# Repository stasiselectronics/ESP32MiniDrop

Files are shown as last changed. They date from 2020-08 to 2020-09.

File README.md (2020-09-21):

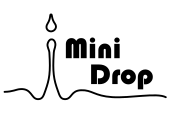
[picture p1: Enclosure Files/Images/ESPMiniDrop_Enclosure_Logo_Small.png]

# ESP32MiniDrop
This repository contains the source files for a DIY Bluetooth connected solenoid controller for use with water drop photography. This project is still a work in progress, so make sure to follow and keep up with any future updates!

[Check out the project's companion page for even more details!](https://chandlermccowan.github.io/ESP32MiniDrop/)

## Quick Links
- [Board Schematics (download)](https://github.com/ChandlerMcCowan/ESP32MiniDrop/raw/master/Hardware%20Files/PDFs/ESP32MiniDrop_Schematics_A02.pdf)
- [Board Drawing (download)](https://github.com/ChandlerMcCowan/ESP32MiniDrop/raw/master/Hardware%20Files/PDFs/ESP32MiniDrop_Assembly_A02.pdf)
- [Enclosure Drawing (download)](https://github.com/ChandlerMcCowan/ESP32MiniDrop/raw/master/Enclosure%20Files/ESP32MiniDrop_Enclosure_Assembly_Drawing.pdf)

## Current Status

This project is still in its early stages, so this repository should be considered a work in progress. As of now, here is what has been done:
- Finalizing schematic and board design for revision A02
- First rounds of iterations on 3D printed parts for enclosure and solenoid stand
- Completed basic function testing for revision A01
- Test firmware developed for ESP32 to use Bluetooth serial communication to pass JSON objects for control and configuration

## Future Goals

Here's what needs to get done for this project:
- Develop firmware to enable connection to Android/iOS app
- Develop Android/iOS app
- Perform electrical tests on board design

## Usage
The goal for this device is to help make water drop photography a snap. Water drop photography focuses on macro shots of water or other liquids at various stages of impact. This controller enables you to use an electronically controlled valve (i.e. solenoid) positioned above a pool of liquid, where you can adjust the timing between succesive drops, the size of the drops themselves, and when to tell the camera to take the picture. By connecting your phone to the controller, you'll be able to dial in these settings and get significantly more repeatable shots than with manual methods.

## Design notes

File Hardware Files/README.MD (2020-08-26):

# ESP32MiniDrop Hardware Files
Designed in KiCad 5.1.6 

This folder contains the source files for the PCB design of the ESP32MiniDrop, along with supporting documentation. Here you can find PDFs of the schematic, an assembly drawing, and gerbers used for fabrication. 

The board design is centered around the ESP32 WROOM 32D module. This has WiFi and Bluetooth included, which helps to reduce the auxillary components needed. The board has one screw terminal to attach bare wires to hook up the solenoid coil. The solenoid is controlled with a MOSFET with flyback diode attached. 

To help load Arduino sketches onto the board, an USB to UART IC is included in the design. This takes the USB data lines and converts them to the RS232 UART signals going to the ESP32. When programming, the script used to flash the chip will take advantage of the DTR and RTS signals to put the EPS32 into boot mode and automatically reset when done. 

**NOTE**
This board uses 0603 passive components and small outline packages, so a patient hand and good eyes (or a microscope) will be needed to hand solder. The CP2012N is in a Quad Flat no Lead (QFN) package, and is not an easy part to attach. You can skip the USB to UART chip and instead use the 0.100" programming headers (J5) to load the sketches on the ESP32 manually.

## Overview
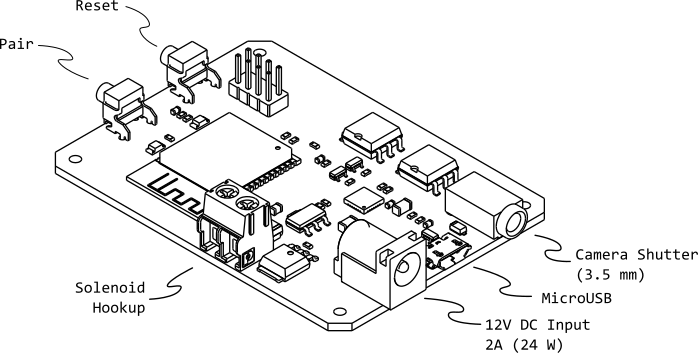
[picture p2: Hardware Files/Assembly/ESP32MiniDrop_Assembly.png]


## Bill of Materials
| Reference Designator | Value | Quantity | Manufacturer | Part Number |
|---|---|:---:|---|---:|
| C1, C3 | 0.1uF 50V | 2 | Yageo | CC0603ZRY5V9BB104 |
| C2, C5, C7 | 10uF 50V | 3 | Samsung Electro-Mechanics | CL31A106MBHNNNE |
| C4 C6 | 1nF 50V | 2 | Yageo | CC0603KRX7R9BB102 |
| C8 | 1uF 50V | 1 | Yageo | CC0603KRX5R9BB105 |
| C9 | 22uF 6.3V | 1 | Samsung Electro-Mechanics | CL21A226MQQNNNE |
| D1, D6 | 40V 2A | 2 | ON Semiconductor | SS24FL |
| D2 | SP0502BAHT | 1 | Littelfuse Inc. | SP0502BAHTG |
| D3 | GREEN 3.2V 20mA | 1 | Wurth Elektronik | 150120GS75000 |
| D4 | BLUE 3.2V 20mA | 1 | Wurth Elektronik | 150120BS75000 |
| D5 | 20V 1A | 1 | ON Semiconductor | MBR120VLSFT3G |
| D7 | 600V 5A | 1 | SMC Diode Solutions | SD560BTR |
| J1 | USB_B_Mini | 1 | Molex | 1050170001 |
| J2 | Barrel_Jack | 1 | CUI Devices | PJ-037A |
| J3 | AudioJack | 1 | Kycon, Inc. | STX-3000 |
| J4 | Solenoid Terminal  | 1 | Pheonix Contact | 1935161 |
| Q1 Q2 | S8050 | 2 | ON Semiconductor | MMBT2222ALT1G |
| Q3 | NMOS 60V 46A | 1 | ON Semiconductor | NTD5865NLT4G |
| R1, R2, R6, R7, R10, R13, R16 | 10k 1% 0.1W | 7 | Yageo | RC0603FR-0710KL |
| R14, R15 | 220R 1% 0.1W | 2 | Yageo | RC0603FR-07220RL |
| R3 | 22.1K 1% 0.1W | 1 | Yageo | RC0603FR-0722K1L |
| R4 | 47.5K 1% 0.1W | 1 | Yageo | RC0603FR-0747K5L |
| R5 | 2K 1% 0.1W | 1 | Yageo | RC0603FR-072KL |
| R8, R9, R11, R12 | 0R 0.1W | 4 | Yageo | 311-0.0GRCT-ND |
| SW1 | SPST (RED) | 1 | TE Connectivity ALCOSWITCH Switches | 1825027-6 |
| SW2 | SPST (BLUE) | 1 | TE Connectivity ALCOSWITCH Switches | 1825027-8 |
| U1 | CP2102N-A01-GQFN28 | 1 | Silicon Labs | CP2102N-A02-GQFN28R |
| U2 | AZ1117-3.3 | 1 | Diodes Incorporated | AZ1117CH-3.3TRG1 |
| U3 | ESP32-WROOM-32 | 1 | Espressif | ESP32-WROOM-32D |
| U4, U5 | 4N25 | 2 | Broadcom Limited | 4N25-500E |

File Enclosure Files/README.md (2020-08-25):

# Enclosure

Designed in FreeCAD 0.18

Here are the design files for a 3D printable plastic enclosure for the ESP32MiniDrop. There are two pieces, a Top and Bottom. STEP files are included to help visualize the pieces, feel free to 

## Printing
To start 3D printing, download the STL Files or modify the CAD files and export to STL.

A test print is planned and will be reported here. 

Using Prusa Slicer 2.2.0 with the following settings gives a print time of 5h 12m
- Layer Height | 0.10mm Detail 
- Filament     | Generic PLA   
- Supports     | None          
- Infill       | 80%           

## Overview
Here is an orhtographic view of the assembled case, along with a size comparison to a Sony DSLR and 12V Solenoid Valve. 

Light pipes for the two status LEDs can be created using 3mm diameter acrylic rods, cut to 12mm and inserted into the top piece.

There are 4 M2 Screw holes that for now just self tap into the top section plastic. Threaded inserts would be great addition, or maybe an embedded nut. Screw length should be between 6mm and 8mm.

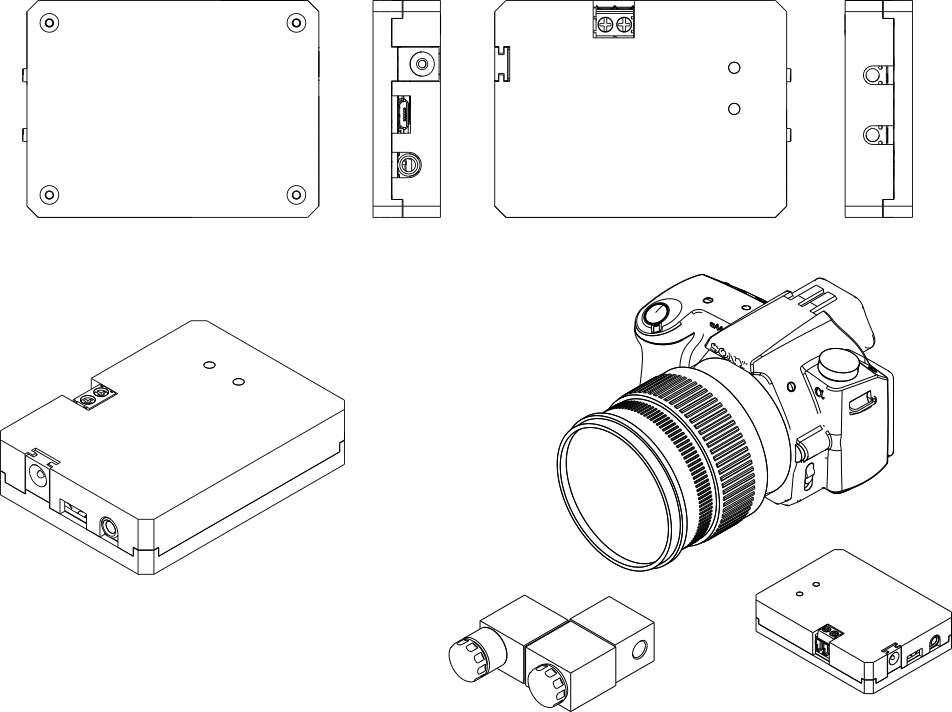
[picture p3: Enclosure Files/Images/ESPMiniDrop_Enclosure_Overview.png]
[]()

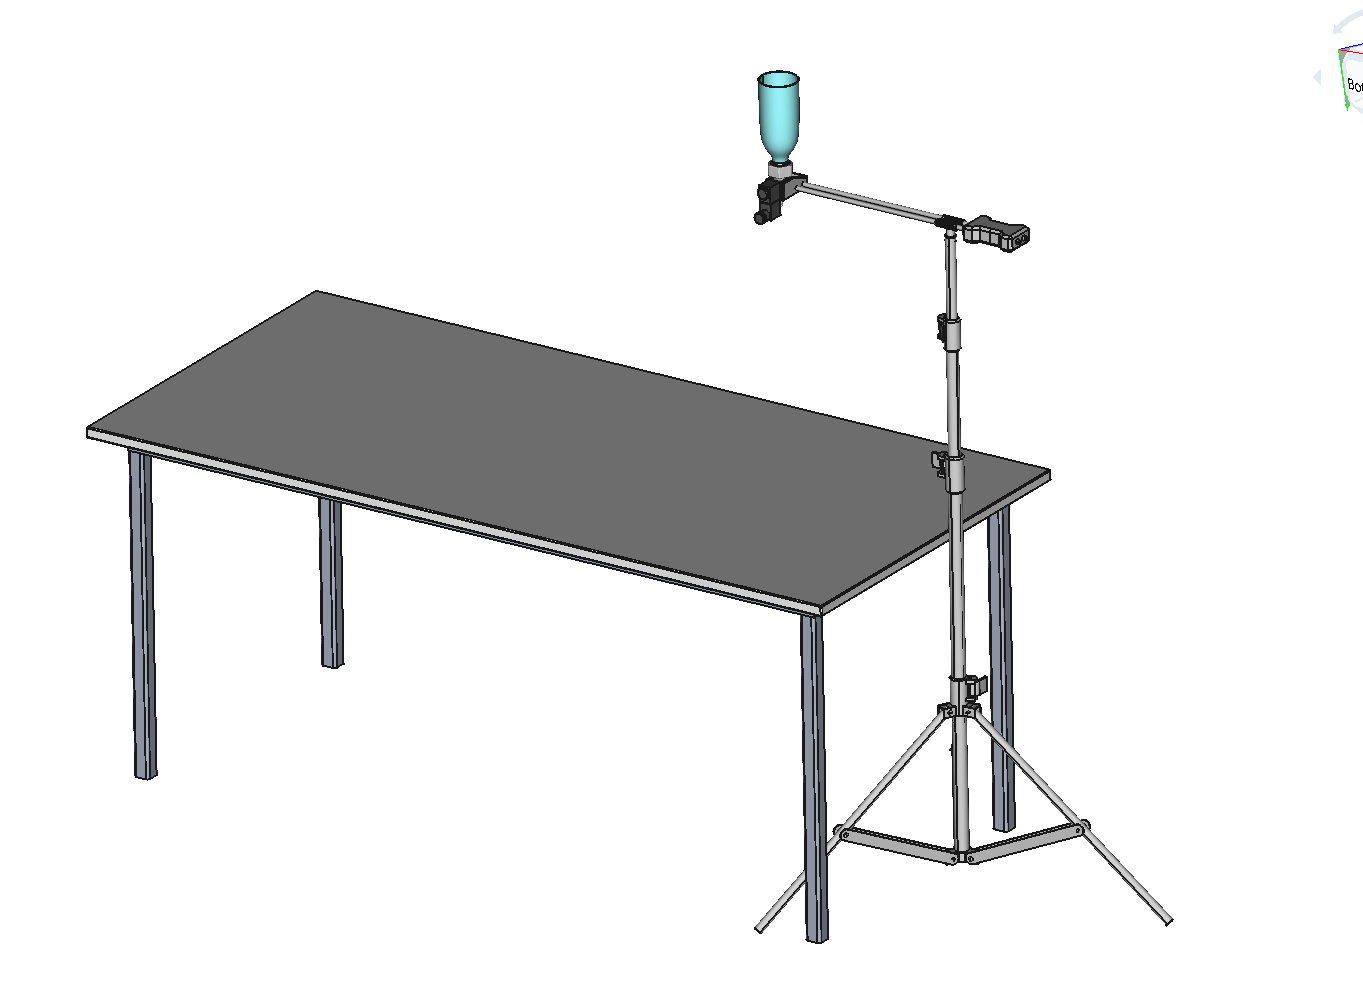
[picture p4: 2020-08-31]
Stand Files/Images/StandWithTable.png

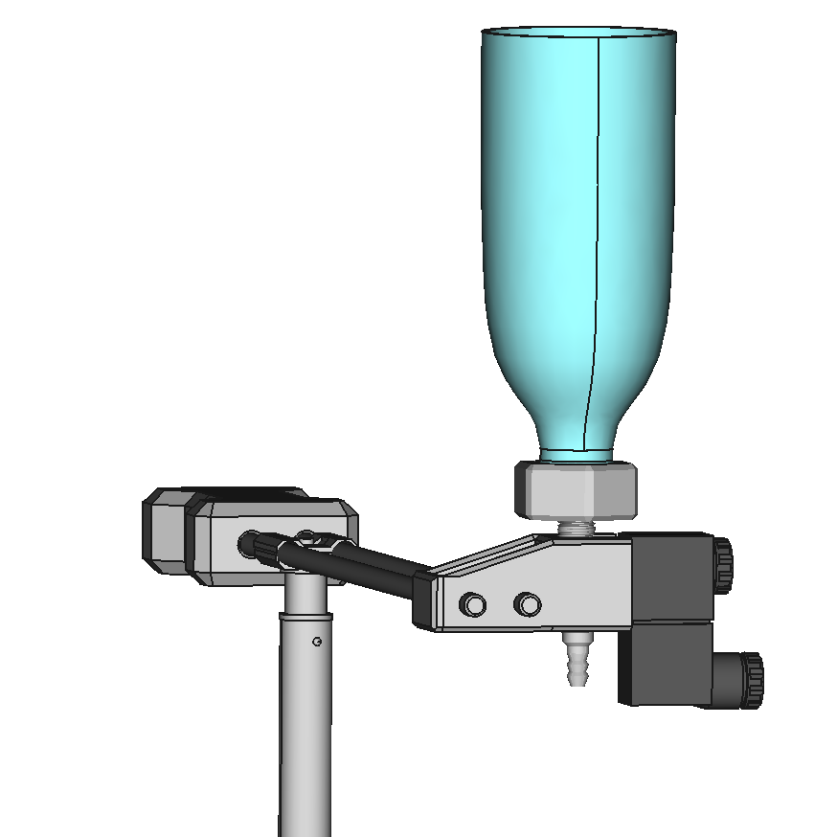
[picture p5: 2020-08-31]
Stand Files/Images/bracke_closeup.png

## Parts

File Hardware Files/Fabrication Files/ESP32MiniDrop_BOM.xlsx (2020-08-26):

Project Name | ESP32MiniDrop | Rev | A02
Reference Designator | Description | Manufactuer | Part Number | Quantity
C1, C3 | 0.1uF 50V | Yageo | CC0603ZRY5V9BB104 | 2
C2, C5, C7 | 10uF 50V | Samsung Electro-Mechanics | CL31A106MBHNNNE | 3
C4 C6 | 1nF 50V | Yageo | CC0603KRX7R9BB102 | 2
C8 | 1uF 50V | Yageo | CC0603KRX5R9BB105 | 1
C9 | 22uF 6.3V | Samsung Electro-Mechanics | CL21A226MQQNNNE | 1
D1, D6 | 40V 2A | ON Semiconductor | SS24FL | 2
D2 | SP0502BAHT | Littelfuse Inc. | SP0502BAHTG | 1
D3 | GREEN 3.2V 20mA | Wurth Elektronik | 150120GS75000 | 1
D4 | BLUE 3.2V 20mA | Wurth Elektronik | 150120BS75000 | 1
D5 | 20V 1A | ON Semiconductor | MBR120VLSFT3G | 1
D7 | 600V 5A | SMC Diode Solutions | SD560BTR | 1
J1 | USB_B_Mini | Molex | 1050170001 | 1
J2 | Barrel_Jack | CUI Devices | PJ-037A | 1
J3 | AudioJack | Kycon, Inc. | STX-3000 | 1
J4 | Solenoid Terminal | Pheonix Contact | 1935161 | 1
Q1 Q2 | S8050 | ON Semiconductor | MMBT2222ALT1G | 2
Q3 | NMOS 60V 46A | ON Semiconductor | NTD5865NLT4G | 1
R1, R2, R6, R7, R10, R13, R16 | 10k 1% 0.1W | Yageo | RC0603FR-0710KL | 7
R14, R15 | 220R 1% 0.1W | Yageo | RC0603FR-07220RL | 2
R3 | 22.1K 1% 0.1W | Yageo | RC0603FR-0722K1L | 1
R4 | 47.5K 1% 0.1W | Yageo | RC0603FR-0747K5L | 1
R5 | 2K 1% 0.1W | Yageo | RC0603FR-072KL | 1
R8, R9, R11, R12 | 0R 0.1W | Yageo | 311-0.0GRCT-ND | 4
SW1 | SPST (RED) | TE Connectivity ALCOSWITCH Switches | 1825027-6 | 1
SW2 | SPST (BLUE) | TE Connectivity ALCOSWITCH Switches | 1825027-8 | 1
U1 | CP2102N-A01-GQFN28 | Silicon Labs | CP2102N-A02-GQFN28R | 1
U2 | AZ1117-3.3 | Diodes Incorporated | AZ1117CH-3.3TRG1 | 1
U3 | ESP32-WROOM-32 | Espressif | ESP32-WROOM-32D | 1
U4, U5 | 4N25 | Broadcom Limited | 4N25-500E | 2

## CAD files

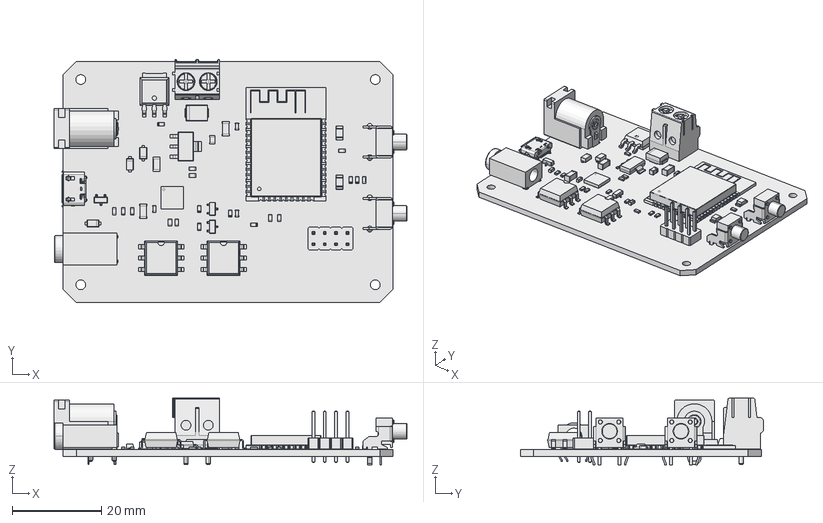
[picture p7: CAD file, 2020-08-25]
Hardware Files/Assembly/ESP32MiniDrop_Assembly.FCStd
79.1 x 54.5 x 14.9 mm

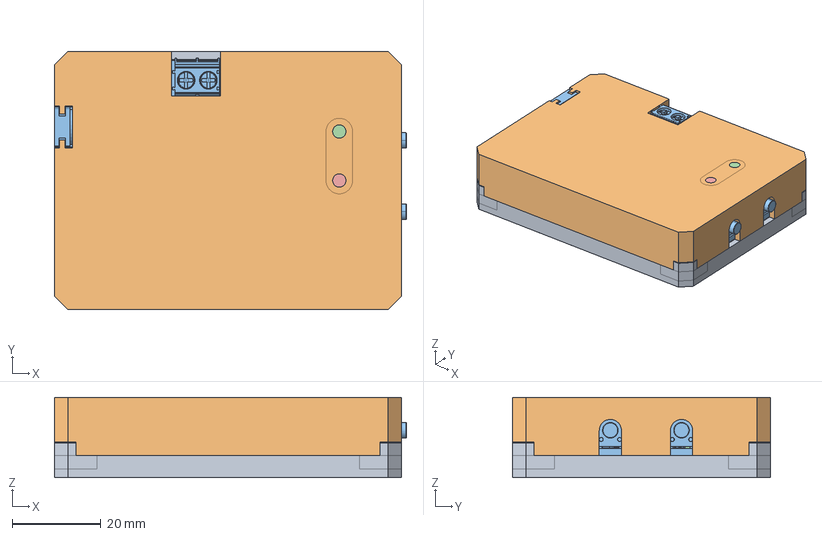
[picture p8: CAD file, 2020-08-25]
Enclosure Files/CAD Files/ESPMiniDrop_Enclosure_Assembly.FCStd
79.1 x 58.0 x 18.1 mm
ESPMiniDrop_Enclosure_Bottom_001
ESPMiniDrop_Enclosure_001
ESP32MiniDrop_PCBA1_001
ESPMiniDrop_Enclosure_LightPipe_001
ESPMiniDrop_Enclosure_LightPipe_002

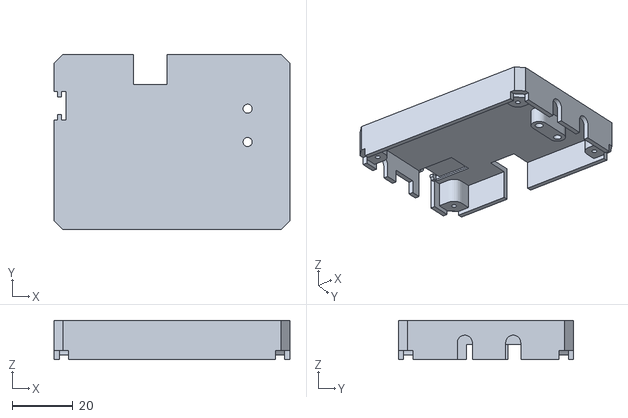
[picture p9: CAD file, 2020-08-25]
Enclosure Files/STL Files/ESP32MiniDrop_Enclosure_Top.stl
78.0 x 58.0 x 13.0

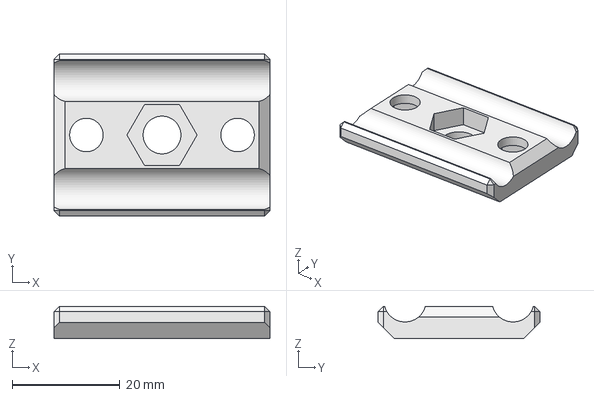
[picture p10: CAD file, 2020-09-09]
Stand Files/CAD Files/ESP32MiniDrop_Stand_TripodClampBtm.FCStd
40.0 x 30.0 x 6.00 mm

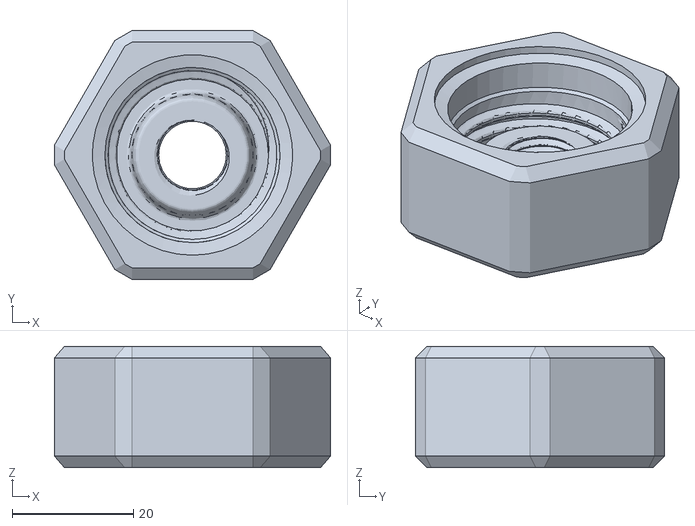
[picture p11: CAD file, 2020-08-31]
Stand Files/STL Files/ESP32MiniDrop_Stand_BottleAdapter.stl
45.4 x 41.0 x 20.0

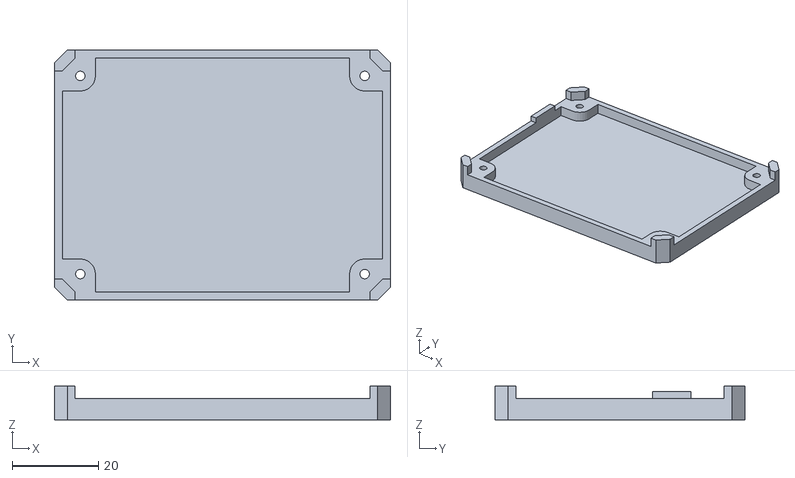
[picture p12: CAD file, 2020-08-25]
Enclosure Files/STL Files/ESP32MiniDrop_Enclosure_Bottom.stl
78.0 x 58.0 x 7.80

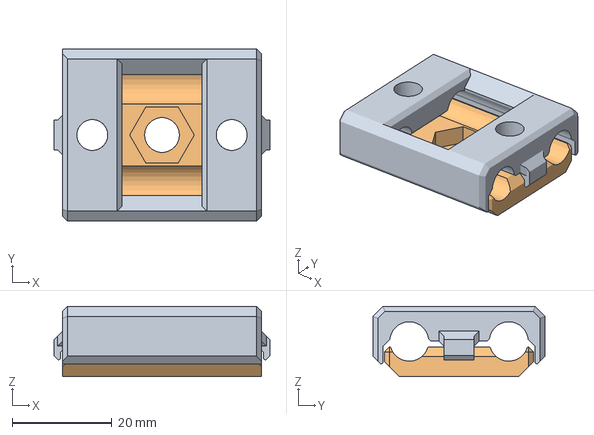
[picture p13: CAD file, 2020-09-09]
Stand Files/CAD Files/ESP32MiniDrop_Stand_TripodClampTop.FCStd
43.4 x 34.6 x 14.1 mm
ESP32MiniDrop_Stand_TripodClampBtm

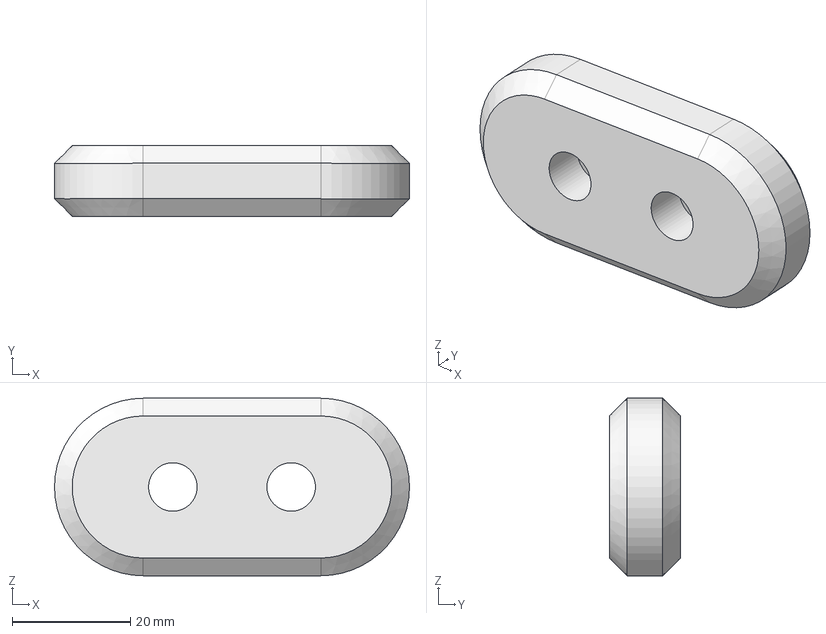
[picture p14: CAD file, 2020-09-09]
Stand Files/CAD Files/ESP32MiniDrop_Stand_RodEnd.FCStd
60.0 x 12.0 x 30.0 mm

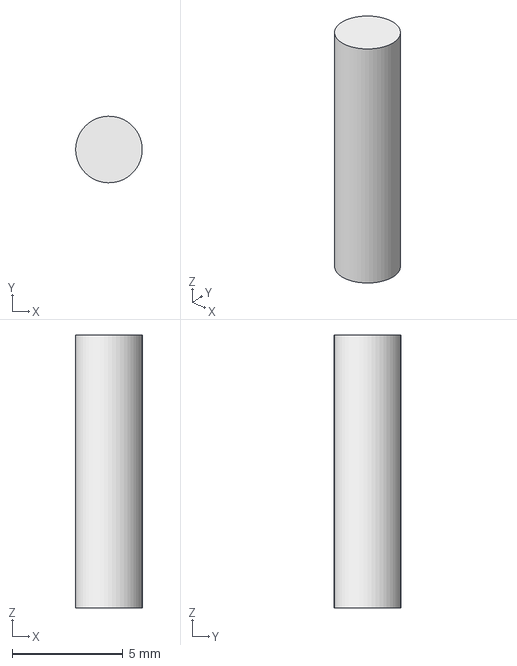
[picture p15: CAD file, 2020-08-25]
Enclosure Files/CAD Files/ESPMiniDrop_Enclosure_LightPipe.FCStd
3.00 x 3.00 x 12.3 mm

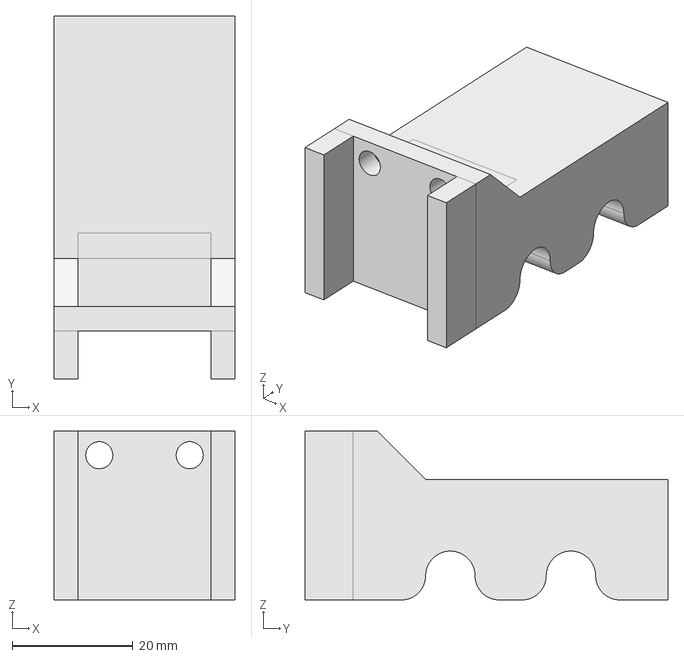
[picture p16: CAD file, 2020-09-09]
Stand Files/CAD Files/ESP32MiniDrop_Stand_SolenoidBracket.FCStd
30.0 x 60.2 x 28.0 mm

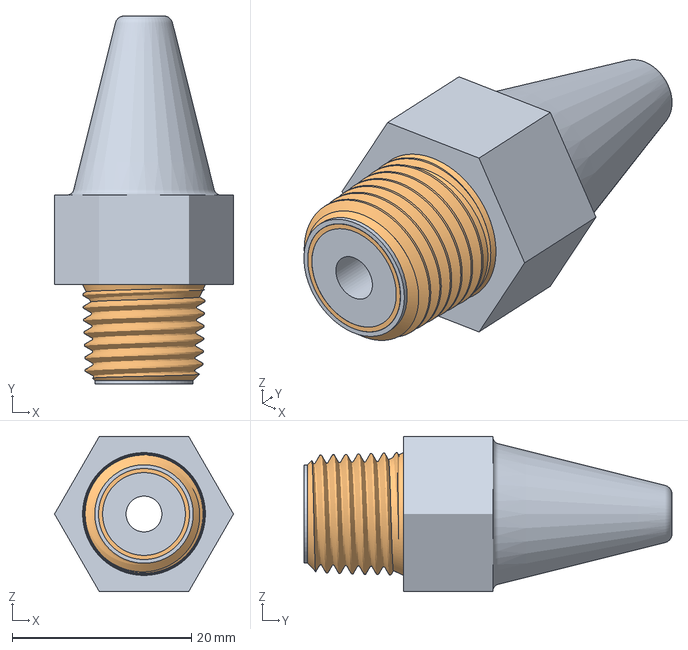
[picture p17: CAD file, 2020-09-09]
Stand Files/CAD Files/ESP32MiniDrop_Stand_SolenoidNozzle.FCStd
20.0 x 41.1 x 17.3 mm
25_npt_close_nipple

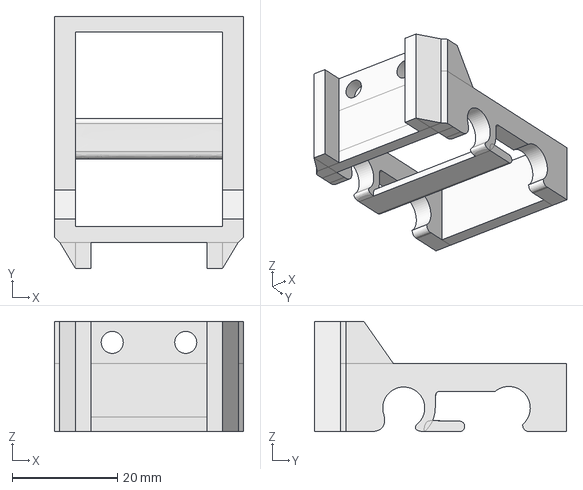
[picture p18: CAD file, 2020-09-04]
Stand Files/CAD Files/ESP32MiniDrop_Stand_SolenoidBracketSnap.FCStd
36.0 x 48.0 x 21.0 mm

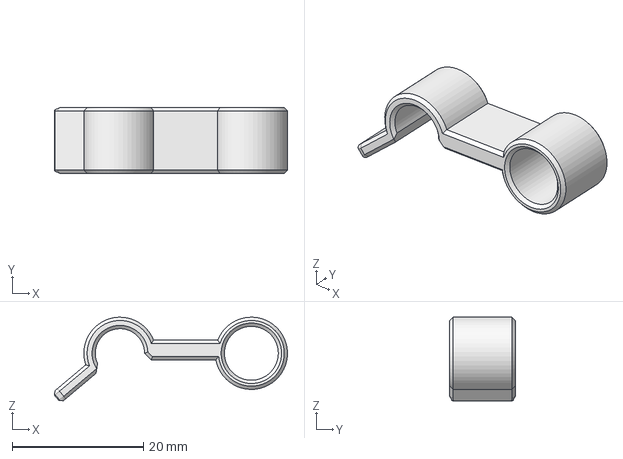
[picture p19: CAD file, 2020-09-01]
Stand Files/CAD Files/ESP32MiniDrop_Stand_RodClip.FCStd
35.5 x 10.0 x 12.7 mm

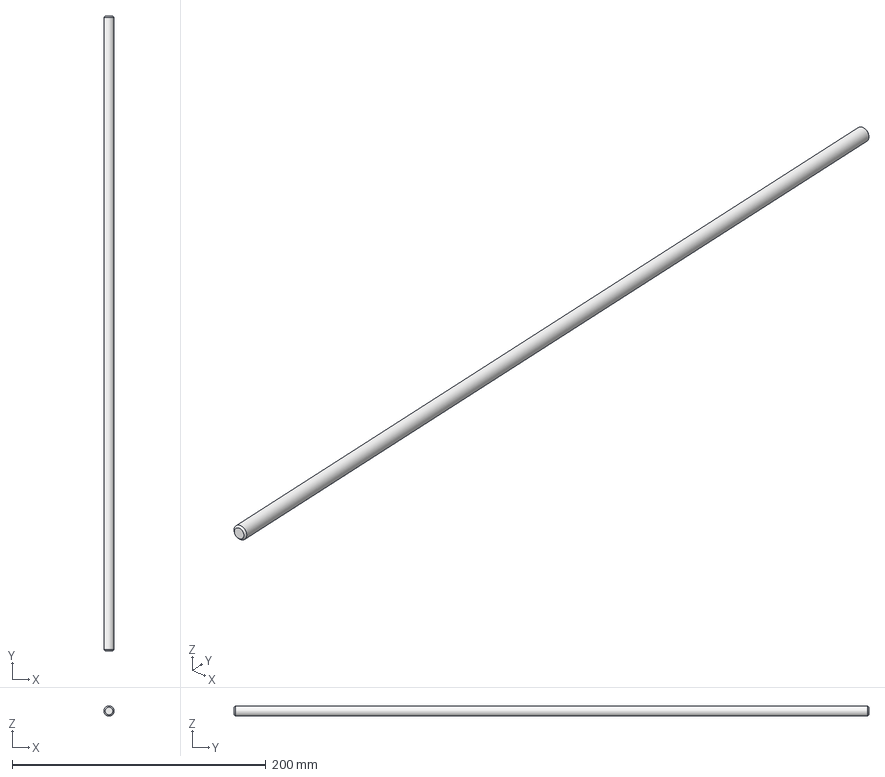
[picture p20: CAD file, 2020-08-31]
Stand Files/CAD Files/ESP32MiniDrop_Stand_M8Rod.FCStd
7.99 x 500.0 x 8.00 mm

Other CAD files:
Enclosure Files/CAD Files/ESPMiniDrop_Enclosure_Drawing.FCStd
Enclosure Files/CAD Files/ESPMiniDrop_Enclosure_Top.FCStd
Enclosure Files/CAD Files/ESPMiniDrop_Enclosure_Bottom.FCStd
Stand Files/CAD Files/ESP32MiniDrop_Stand_CounterWeight.FCStd
Stand Files/STL Files/ESP32MiniDrop_Stand_CounterWeight.stl
Stand Files/STL Files/ESP32MiniDrop_Stand_RodClip.stl
Stand Files/STL Files/ESP32MiniDrop_Stand_RodEnd.stl
Stand Files/STL Files/ESP32MiniDrop_Stand_SolenoidBracket.stl
Stand Files/STL Files/ESP32MiniDrop_Stand_SolenoidBracketSnap.stl
Stand Files/STL Files/ESP32MiniDrop_Stand_SolenoidNozzle.stl
Stand Files/STL Files/ESP32MiniDrop_Stand_TripodClampBtm.stl
Stand Files/STL Files/ESP32MiniDrop_Stand_TripodClampTop.stl

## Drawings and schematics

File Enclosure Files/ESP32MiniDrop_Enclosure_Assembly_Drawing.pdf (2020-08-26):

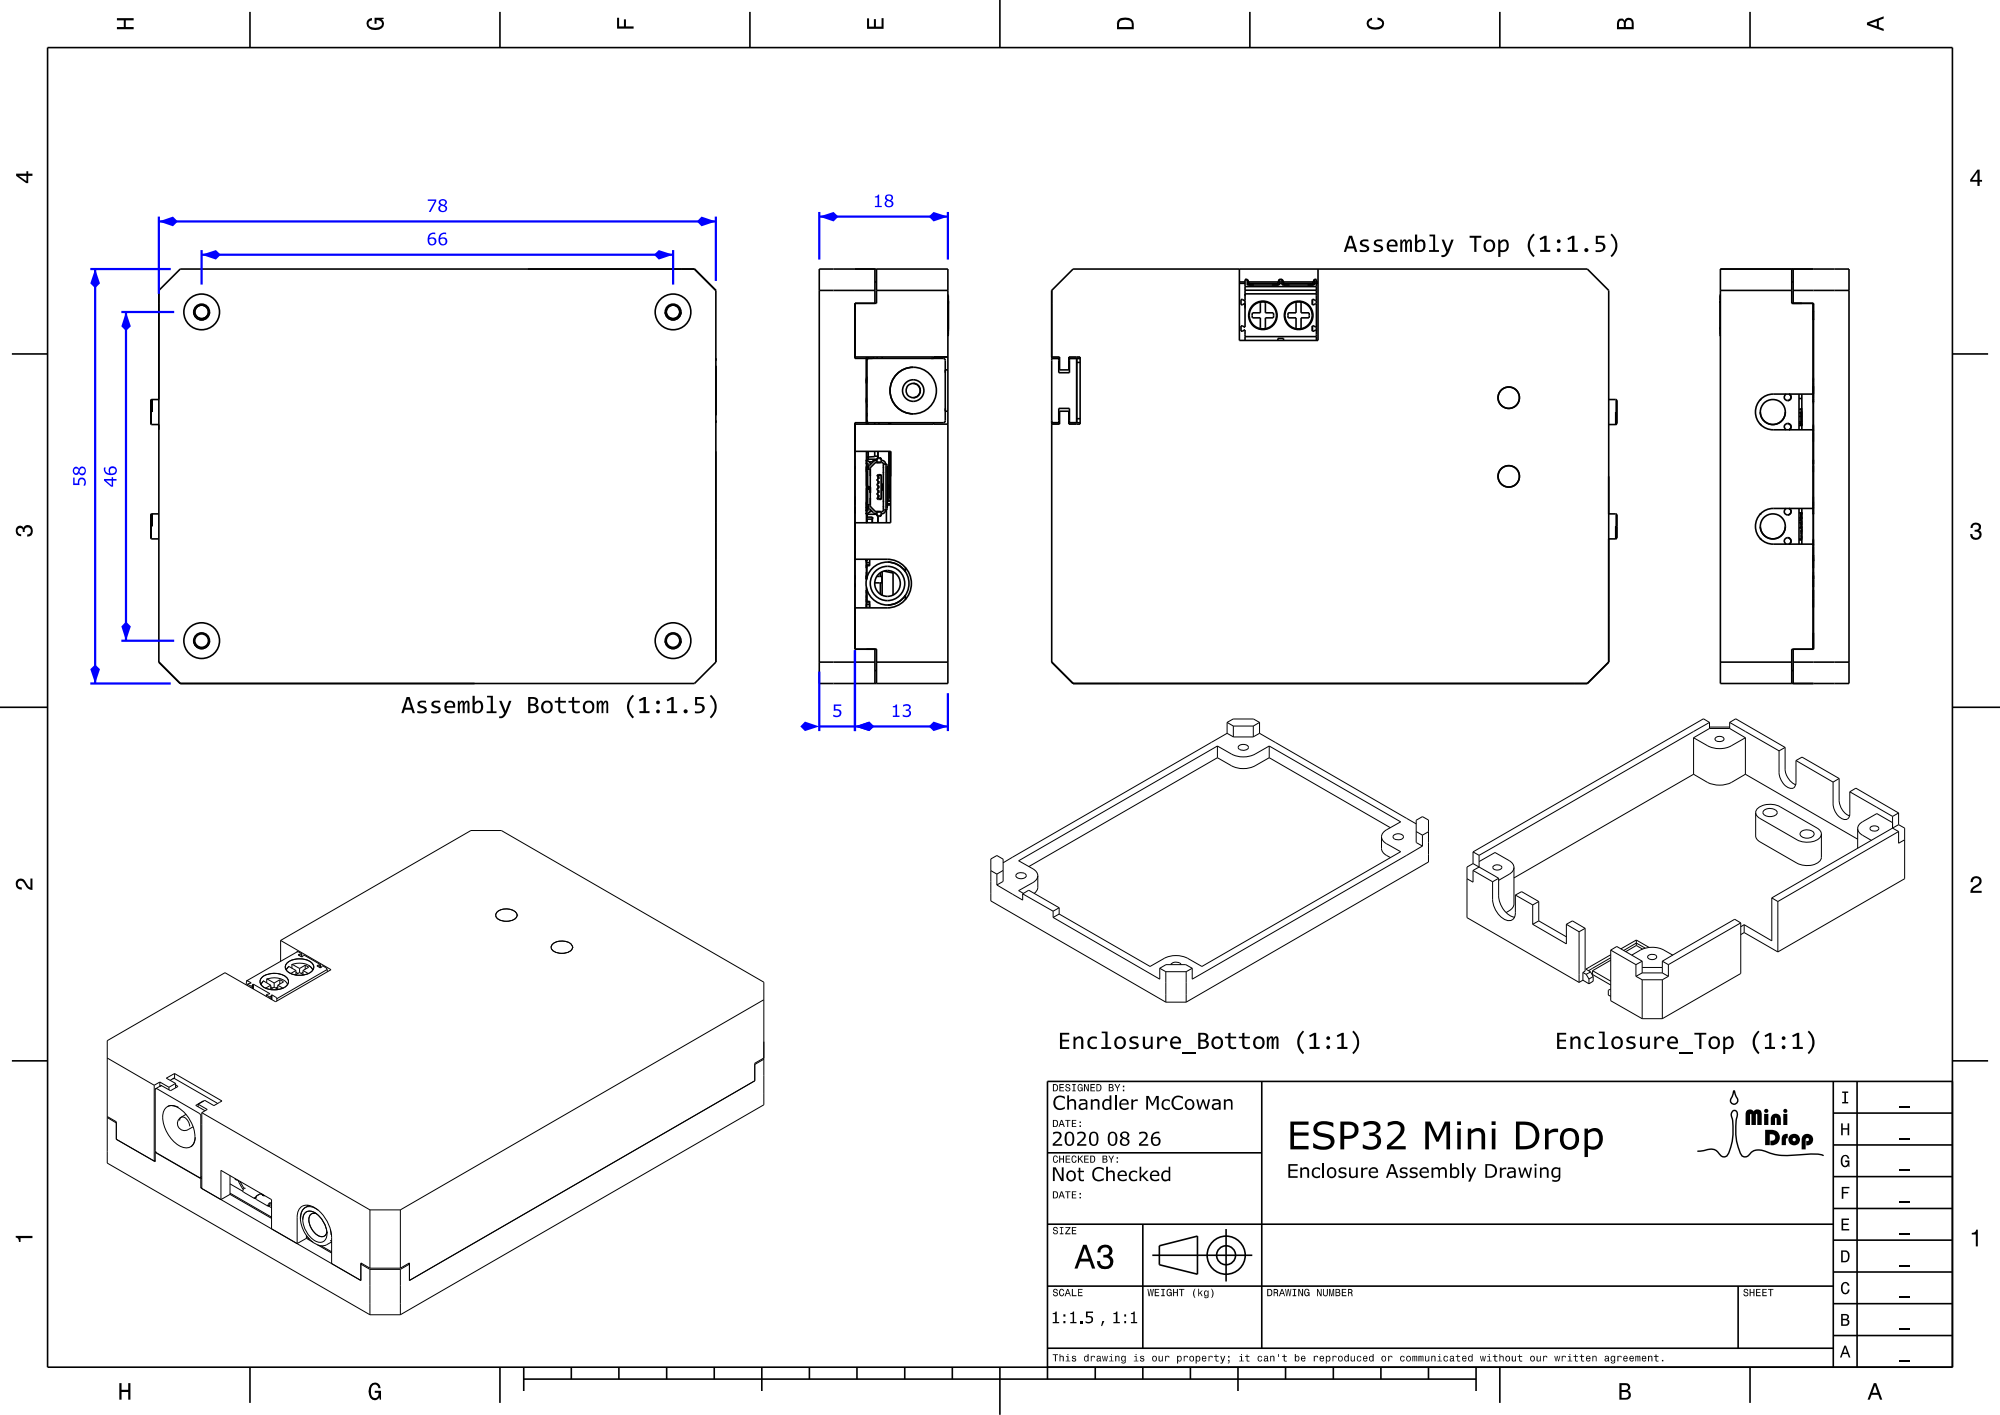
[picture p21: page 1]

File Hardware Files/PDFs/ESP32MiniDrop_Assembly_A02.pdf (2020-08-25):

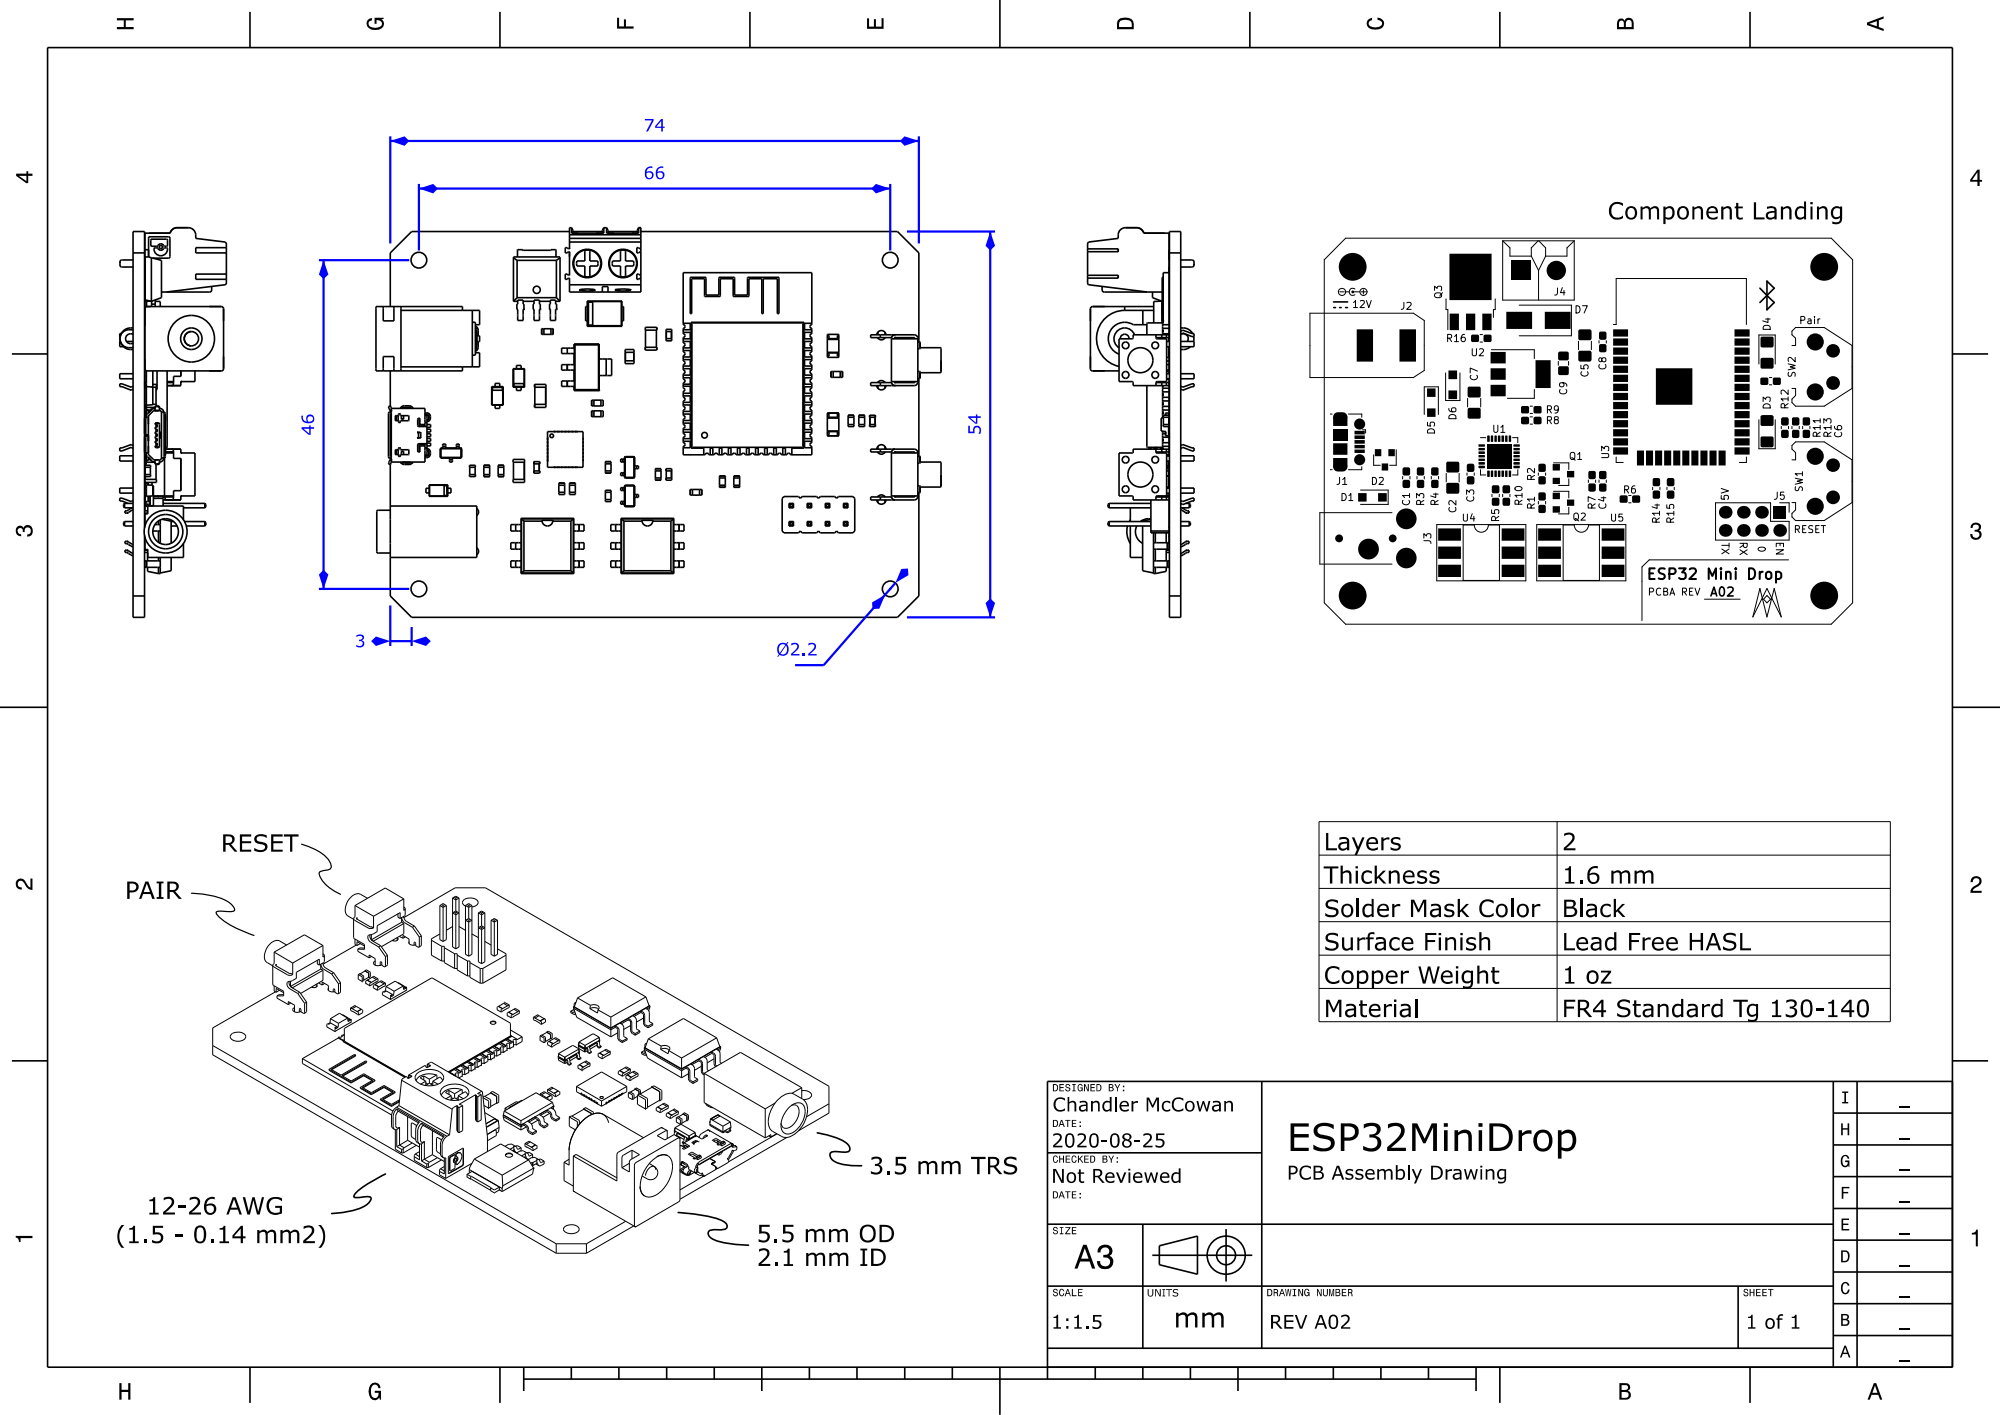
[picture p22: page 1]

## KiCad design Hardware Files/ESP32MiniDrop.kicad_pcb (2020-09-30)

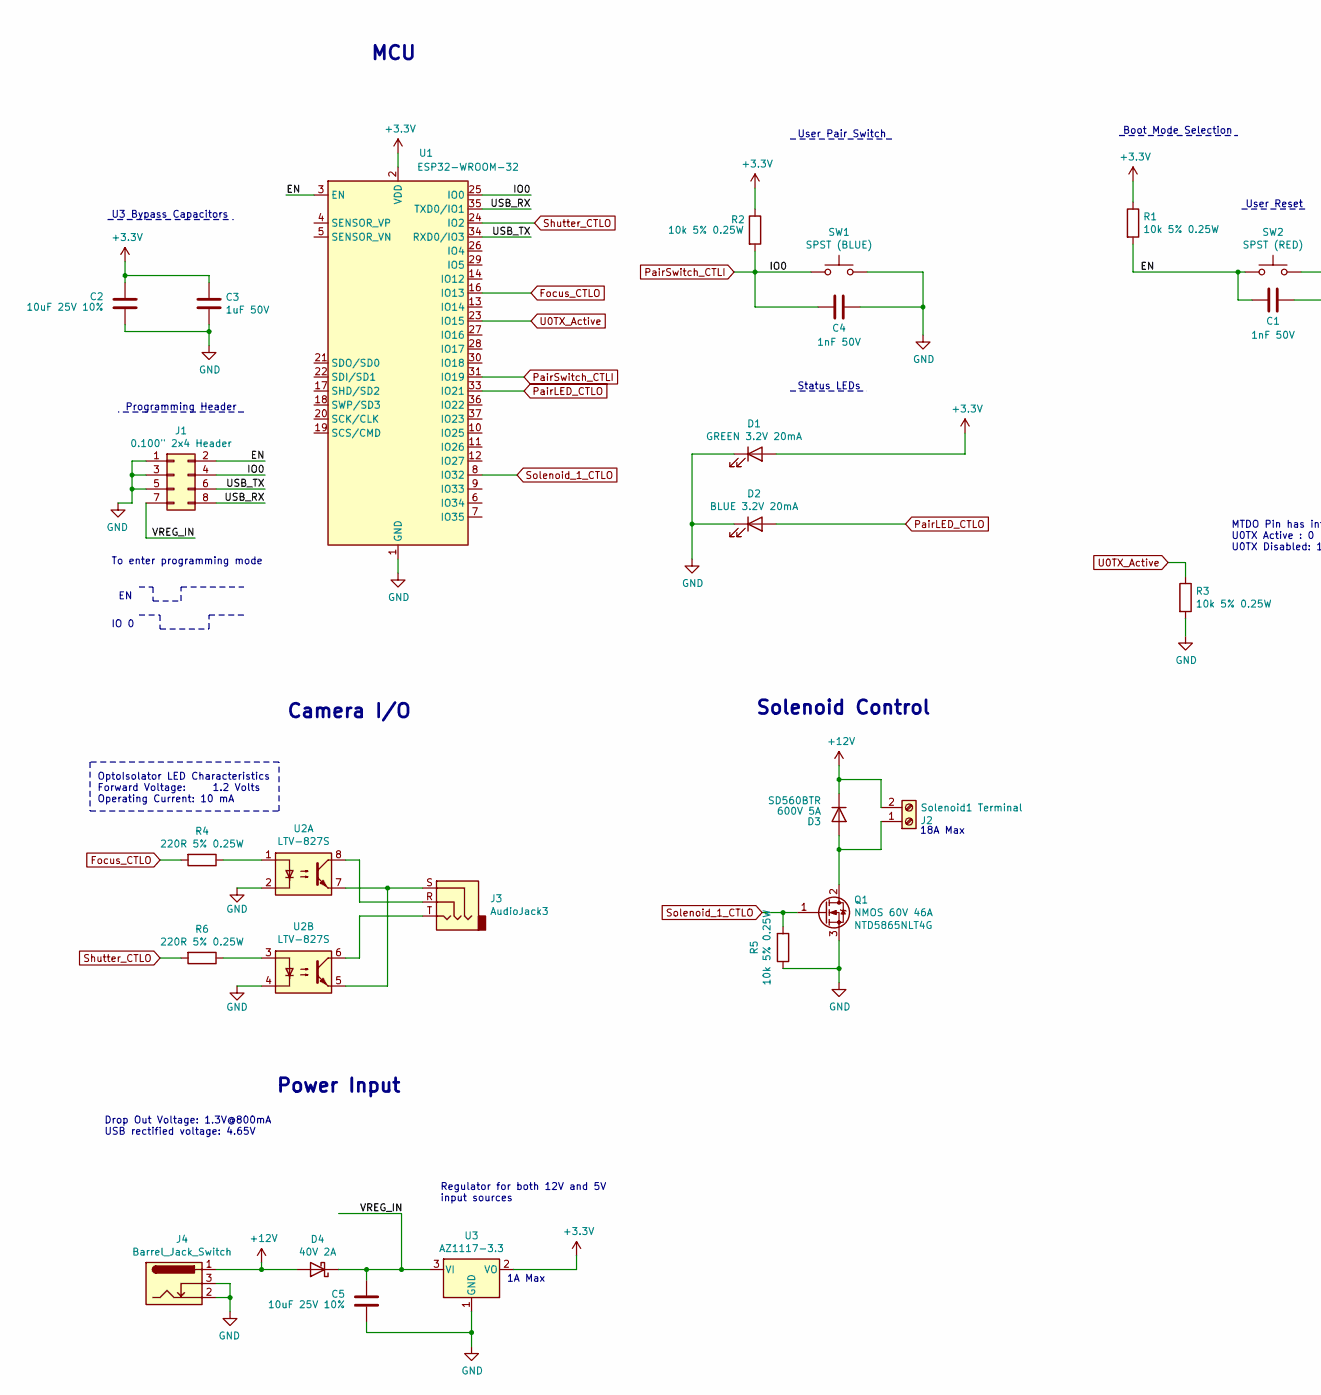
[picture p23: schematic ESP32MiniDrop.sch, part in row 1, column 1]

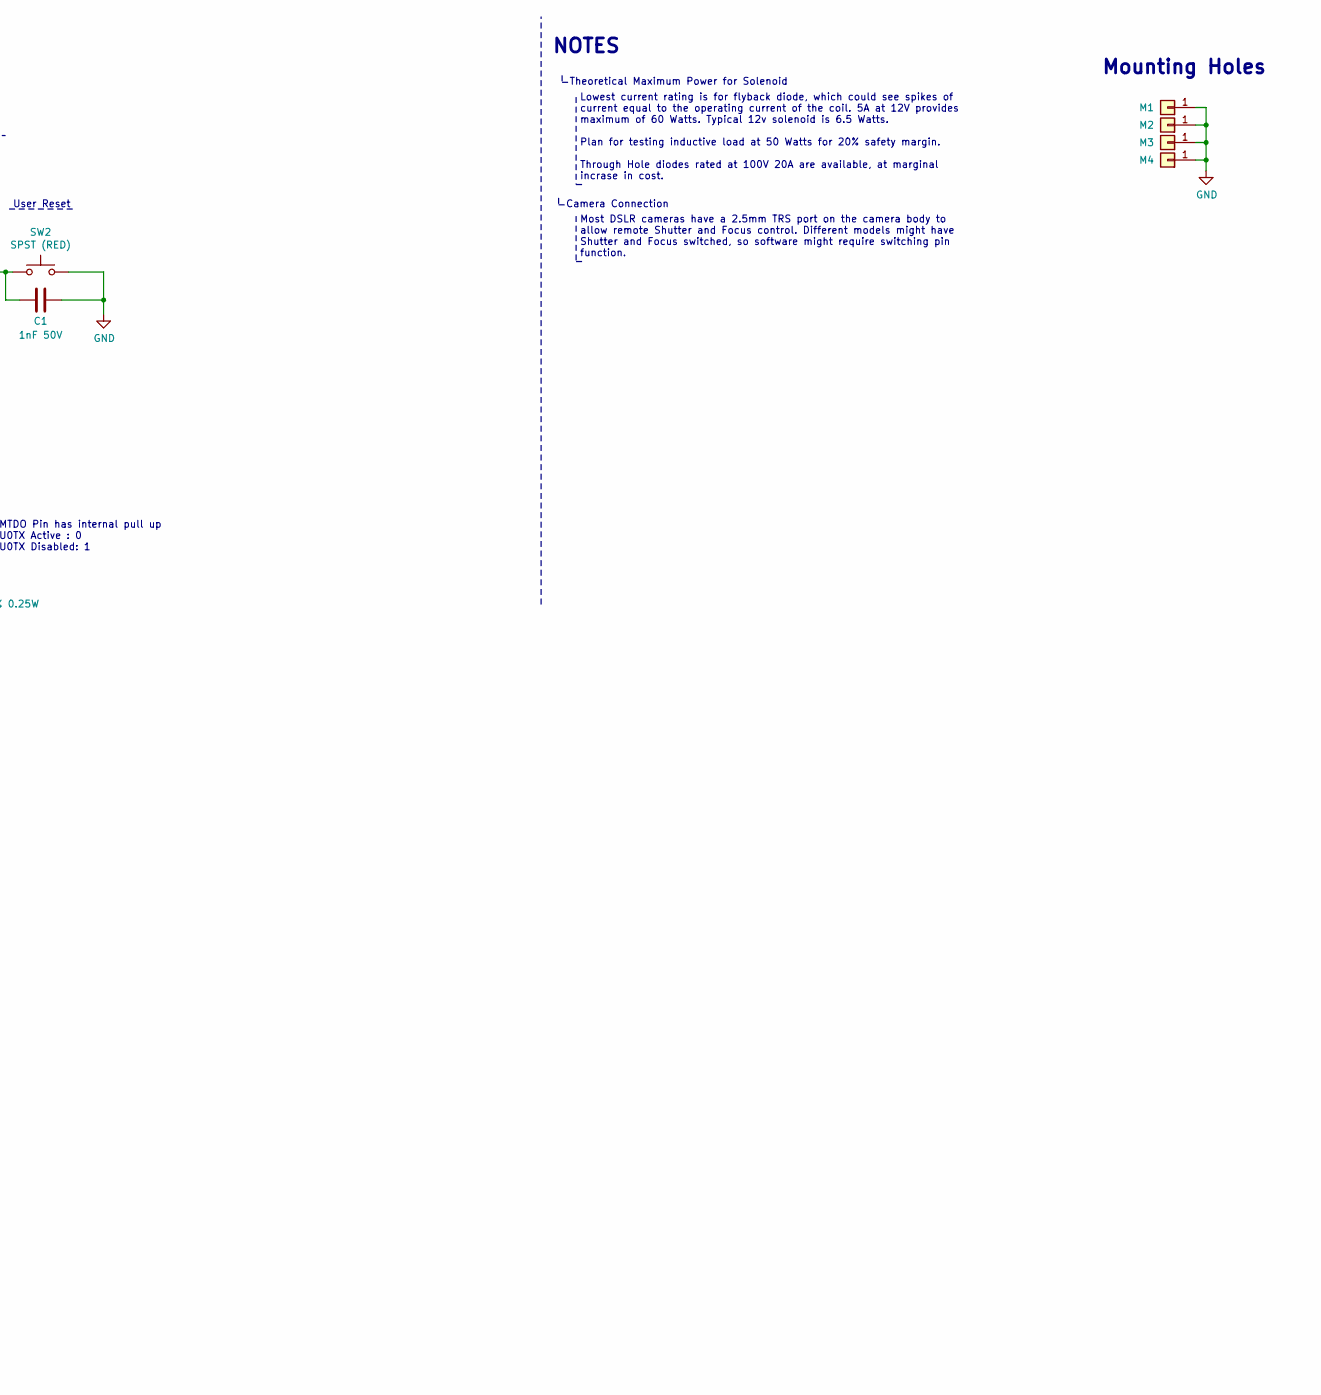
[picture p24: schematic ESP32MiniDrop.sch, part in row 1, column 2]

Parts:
C1, C4: 1nF 50V; C_1206_3216Metric_Pad1.42x1.75mm_HandSolder; MPN 1206B102K500CT
C2, C5: 10uF 25V 10%; C_1206_3216Metric_Pad1.42x1.75mm_HandSolder; MPN CL31A106MAHNNNE
C3: 1uF 50V; C_1206_3216Metric_Pad1.42x1.75mm_HandSolder; MPN CL31B105KBHNFNE
D1: GREEN 3.2V 20mA; LED_1206_3216Metric_Pad1.42x1.75mm_HandSolder; MPN 150120GS75000
D2: BLUE 3.2V 20mA; LED_1206_3216Metric_Pad1.42x1.75mm_HandSolder; MPN 150120BS75000
D3: 600V 5A; D_SMB_Handsoldering; MPN SD560BTR
D4: 40V 2A; D_SOD-123F; MPN SS24FL
J1: 0.100\" 2x4 Header; PinHeader_2x04_P2.54mm_Vertical
J2: Solenoid1 Terminal; 1935161; MPN 1935161
J3: AudioJack3; SJ1-3523N; MPN SJ1-3523N
J4: Barrel_Jack_Switch; BarrelJack_Wuerth_6941xx301002_3D
M1, M2, M3, M4: Conn_01x01; MountingHole_3.2mm_M3_ISO7380_Pad
Q1: NMOS 60V 46A; TO-252-3_TabPin2; MPN NTD5865NLT4G
R1, R2, R3, R5: 10k 5% 0.25W; R_1206_3216Metric_Pad1.42x1.75mm_HandSolder; MPN RC1206JR-0710KL
R4, R6: 220R 5% 0.25W; R_1206_3216Metric_Pad1.42x1.75mm_HandSolder; MPN RC1206JR-07220RL
SW1: SPST (BLUE); 1825027-8; MPN 1825027-8
SW2: SPST (RED); 1825027-8; MPN 1825027-6
U1: ESP32-WROOM-32; MPN ESP32-WROOM-32D
U2: LTV-827S; SMDIP-8_W9.53mm
U3: AZ1117-3.3; SOT-223-3_TabPin2; MPN AZ1117CH-3.3TRG1

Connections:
+3V3: C2.2, C3.1, D1.2 (A), R1.1, R2.1, U1.2 (VDD), U3.2 (VO)
+12V: D3.1 (K), D4.2 (A), J2.2, J4.1
/EN: C1.2, J1.2, R1.2, SW2.1, U1.3 (EN)
/USB_RX: J1.8, U1.35 (TXD0/IO1)
/USB_TX: J1.6, U1.34 (RXD0/IO3)
/VREG_IN: C5.2, D4.1 (K), J1.7, U3.3 (VI)
Focus_CTLO: R4.2, U1.16 (IO13)
GND: C1.1, C2.1, C3.2, C4.1, C5.1, D1.1 (K), D2.1 (K), J1.1, J1.3, J1.5, J4.2, J4.3, M1.1, M2.1, M3.1, M4.1, Q1.3 (S), R3.2, R5.1, SW1.2, SW2.2, U1.1 (GND), U1.15 (GND), U1.38 (GND), U1.39 (GND), U2.2, U2.4, U3.1 (GND)
unnamed: D3.2 (A), J2.1, Q1.2 (D)
unnamed: J3.R, U2.8
unnamed: J3.S, U2.5, U2.7
unnamed: J3.T, U2.6
unnamed: R4.1, U2.1
unnamed: R6.1, U2.3
PairLED_CTLO: D2.2 (A), U1.33 (IO21)
PairSwitch_CTLI: C4.2, J1.4, R2.2, SW1.1, U1.25 (IO0), U1.31 (IO19)
Shutter_CTLO: R6.2, U1.24 (IO2)
Solenoid_1_CTLO: Q1.1 (G), R5.2, U1.8 (IO32)
U0TX_Active: R3.1, U1.23 (IO15)

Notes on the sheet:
Regulator for both 12V and 5V input sources
Boot Mode Selection
User Reset
Drop Out Voltage: 1.3V@800mA USB rectified voltage: 4.65V
OptoIsolator LED Characteristics Forward Voltage: 1.2 Volts Operating Current: 10 mA
U3 Bypass Capacitors
Status LEDs
User Pair Switch
Power Input
Camera I/O
Solenoid Control
Programming Header
MCU
NOTES
Theoretical Maximum Power for Solenoid
18A Max
Lowest current rating is for flyback diode, which could see spikes of current equal to the operating current of the coil. 5A at 12V provides maximum of 60 Watts. Typical 12v solenoid is 6.5 Watts. Plan for testing inductive load at 50 Watts for 20% safety margin. Through Hole diodes rated at 100V 2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
Camera Connection
Most DSLR cameras have a 2.5mm TRS port on the camera body to allow remote Shutter and Focus control. Different models might have Shutter and Focus switched, so software might require switching pin function.
IO 0
To enter programming mode
1A Max
Mounting Holes
MTDO Pin has internal pull up U0TX Active : 0 U0TX Disabled: 1

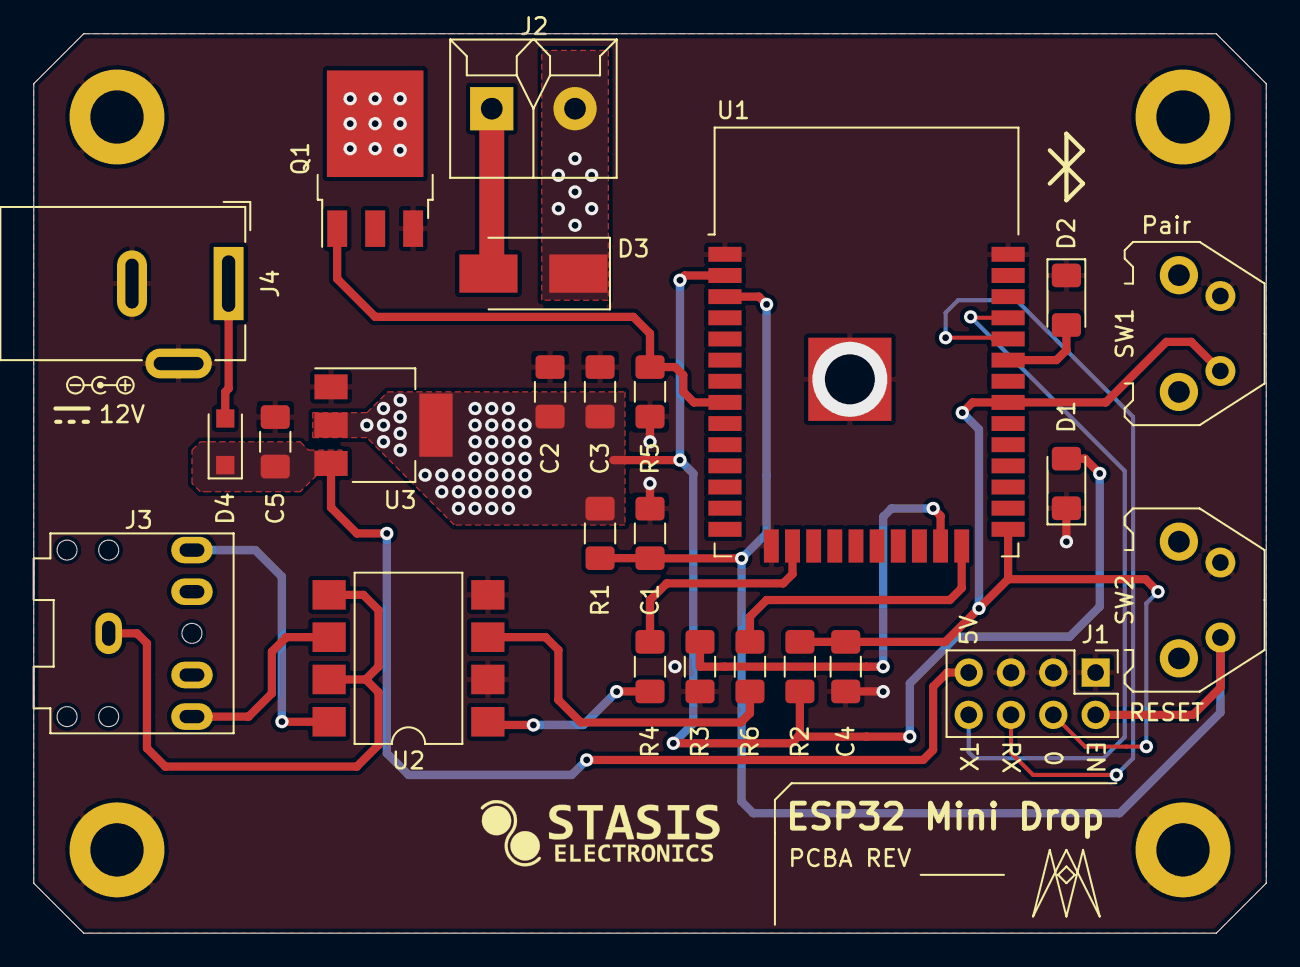
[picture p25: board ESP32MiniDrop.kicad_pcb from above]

Board: 2 copper layers, 74.0 x 54.0 mm, 29 parts (0 on the bottom side), 19 nets.

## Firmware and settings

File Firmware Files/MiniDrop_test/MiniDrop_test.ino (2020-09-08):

  #include <ArduinoJson.h>
#include "BluetoothSerial.h"

// GPIO Definitions
#define BTN_PAIR 19
#define LED_PAIR 21
#define SHUTTER_CTLO 13
#define FOCUS_CTLO 15
#define SOLENOID_CTLO 32


#if !defined(CONFIG_BT_ENABLED) || !defined(CONFIG_BLUEDROID_ENABLED)
#error Bluetooth is not enabled! Please run `make menuconfig` to and enable it
#endif


BluetoothSerial SerialBT;
StaticJsonDocument<5096> doc;
char bluetooth_buffer[1024]; // parsing buffer
unsigned bluetooth_i = 0;
int connected_devices = 0;
// Structure to hold options for a water droplet
// Size is how long in ms the solenoid is "on"
// delay is how long it waits until activating the solenoid in ms
struct droplet_struct{
  unsigned size_ms;
  unsigned delay_ms;
};

// structure to hold options for activating the shutter
// right now it is just the delay until activation in ms
struct camera_struct{
  unsigned delay_ms;
};

// structure to hold options for actions
// Includes both droplet and camera structs, so be careful when performing actions
enum action_type{type_none,type_droplet,type_camera};
struct action{
  action_type type;
  droplet_struct droplet;
  camera_struct camera;
};

// Structure array to hold all of our actions
// chosing a very high number of elements just for fun
struct action playlist[5096];
unsigned playlist_i = 0;


void add_action(action myaction){
  playlist[playlist_i]=myaction;
  playlist_i++;
  if(playlist_i >5096)
    playlist_i = 0;
}

void drop(unsigned delay_ms, unsigned size_ms){
  Serial.print("size: ");Serial.print(size_ms);
  Serial.print(" , delay: ");Serial.println(delay_ms);
  // Here we will drop the given droplet
  delay(delay_ms);
  // turn on solenoid
  digitalWrite(SOLENOID_CTLO, HIGH);
  delay(size_ms);
  // turn off solenoid
  digitalWrite(SOLENOID_CTLO, LOW);
}

void expose(unsigned delay_ms){
  Serial.print("delay: ");Serial.println(delay_ms);
  // Here we will take a picture, or "exposure"
  delay(delay_ms);
  // turn on solenoid
  digitalWrite(SHUTTER_CTLO, HIGH);
  delay(300);
  digitalWrite(SHUTTER_CTLO, LOW);
}

void play(){
  Serial.println("---------------------------");
  Serial.println("----------Action!----------");
  Serial.println("---------------------------");
  for(int i = 0; i < playlist_i;i++){
    Serial.print("Action: ");Serial.println(i);
    Serial.print("Action Type: ");
    if(playlist[i].type == type_camera){
      Serial.println("Camera");
      expose(playlist[i].camera.delay_ms);
    }
    if(playlist[i].type == type_droplet){
      Serial.println("Drop");
      drop(playlist[i].droplet.delay_ms, playlist[i].droplet.size_ms);
    }
  }
  playlist_i = 0;
}

void parse_bt(){
  // Here we will parse out a bluetooth message.
  // Serial.print(bluetooth_buffer);
  bluetooth_i = 0; // reset bluetooth message buffer
  // Deserialize the JSON document
  DeserializationError error = deserializeJson(doc, bluetooth_buffer);
  
  // Test if parsing succeeds.
  if (error) {
    Serial.print(F("deserializeJson() failed: "));
    Serial.println(error.c_str());
    return;
  }
  
  // Fetch values
  // Get a reference to the root array
  JsonArray arr = doc.as<JsonArray>();
  for (JsonObject action : arr) {
    String type = action["type"];
    unsigned delay_ms = action["delay"];
    unsigned size_ms = action["size"];
    String hold_status = action["hold_status"];
    struct action myaction; // action structure to hold all the values
    if(type=="droplet"){
      myaction.type= type_droplet;
      myaction.droplet.size_ms = size_ms;
      myaction.droplet.delay_ms = delay_ms;
      add_action(myaction);
    }
    else if(type=="camera"){
      myaction.type= type_camera;
      myaction.camera.delay_ms = delay_ms;
      add_action(myaction);
    }
    else if(type=="hold"){
      if(hold_status=="on"){
        // turn on solenoid
        Serial.println("Keeping Solenoid On");
        digitalWrite(SOLENOID_CTLO, HIGH);
      }
      else if(hold_status=="off"){
        // turn off solenoid
        Serial.println("Turning off Solenoid");
        digitalWrite(SOLENOID_CTLO, LOW);
      }
    }
    else {
      Serial.print("can't determine type: ");Serial.println(type);
    }
  }
  if(playlist_i>0){
    // Now we have finished parsing and adding all actions
    play(); // execute all the actions that were added 
  }
  
}

void callback(esp_spp_cb_event_t event, esp_spp_cb_param_t *param){
// Callback function implementation
  if(event == ESP_SPP_SRV_OPEN_EVT){
    Serial.println("Client Connected");
    connected_devices++;
    digitalWrite(LED_PAIR,HIGH);
  }
  else if(event == ESP_SPP_CLOSE_EVT ){
    Serial.println("Client disconnected");
    connected_devices--;
    if(connected_devices<=0){
      connected_devices=0;
      digitalWrite(LED_PAIR,LOW);
    }
  }
}

void setup() {
  Serial.begin(115200);
  SerialBT.begin("MiniDrop"); //Bluetooth device name
  Serial.println("Initializing MiniDrop");
  
  // Setup GPIO
  pinMode(BTN_PAIR, INPUT);
  pinMode(LED_PAIR, OUTPUT);
  pinMode(SHUTTER_CTLO, OUTPUT);
  pinMode(FOCUS_CTLO, OUTPUT);
  pinMode(SOLENOID_CTLO, OUTPUT);
  pinMode(13,OUTPUT);
  SerialBT.register_callback(callback);
  // Go ahead and turn off the solenoid just in case
  digitalWrite(SOLENOID_CTLO, LOW);
}

void loop() {
  if (SerialBT.available()) {
    char mychar = SerialBT.read();
    bluetooth_buffer[bluetooth_i]=mychar;
    bluetooth_i++;
    //Serial.print(mychar);
    if(mychar==10) // line feed
    {
      //Serial.println("found message");
      parse_bt();
    }
  }
  int i = 1 +2; //busy work to keep alive
}

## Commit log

2020-08-23 Added B.SilkS layer to output
    [ESP32MiniDrop-B_Cu.gbr, ESP32MiniDrop-B_Mask.gbr, ESP32MiniDrop-Edge_Cuts.gbr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]
2020-08-23 Fixed Missing References on PCB
    [ESP32MiniDrop-B_Cu.gbr, ESP32MiniDrop-B_Mask.gbr, ESP32MiniDrop-Edge_Cuts.gbr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]
2020-08-23 Updated Gerber Settings
    [ESP32MiniDrop.kicad_pcb]
2020-08-25 Add missing silkskreen gerber
    [ESP32MiniDrop-B_SilkS.gbr]
2020-08-25 Cleanup Schematics
    [ESP32MiniDrop.kicad_pcb, ESP32MiniDrop.sch]
2020-08-25 Add Schematic PDF
2020-08-25 Add Assembly Files
    [ESP32MiniDrop_Assembly.FCStd]
2020-08-25 Adding Assembly Files
    [ESP32MiniDrop_Assembly.FCStd]
2020-08-25 Add Assembly PNG
2020-08-25 Add Assembly PDF
2020-08-25 Update Assembly PNG
2020-08-25 Changed Programming Header to Virtual
    [ESP32MiniDrop.kicad_pcb]
2020-08-25 Add PCBA 3D Model
2020-08-25 Added Enclosure Top CAD File
    [ESPMiniDrop_Enclosure_Top.FCStd]
2020-08-25 Updated Geometries
    [ESPMiniDrop_Enclosure_Top.FCStd]
2020-08-25 Added Bottom Enclosure CAD File
    [ESPMiniDrop_Enclosure_Bottom.FCStd, ESPMiniDrop_Enclosure_Top.FCStd]
2020-08-25 Geometry Updates
    [ESPMiniDrop_Enclosure_Bottom.FCStd, ESPMiniDrop_Enclosure_Top.FCStd]
2020-08-25 Added STL Files
    [ESP32MiniDrop_Enclosure_Bottom.stl, ESP32MiniDrop_Enclosure_Top.stl, ESPMiniDrop_Enclosure_Top.FCStd]
2020-08-25 Added Enclosure Images
2020-08-26 Added Dimensions & Separate Pieces
    [ESPMiniDrop_Enclosure_Drawing.FCStd]
2020-08-26 Add Assembly Drawing PDF
2020-08-26 Update BOM
    [ESP32MiniDrop_BOM.xlsx]
2020-08-26 Update wrong PN for Green LED
    [ESP32MiniDrop.sch, ESP32MiniDrop_BOM.xlsx]
2020-08-26 Update project footprint library
    [ESP32MiniDrop.kicad_pcb, ESP32MiniDrop.sch]
2020-08-27 Change Schematics to Color
2020-08-27 Rename FAB folder to Fabrication Files
    [ESP32MiniDrop-B_Cu.gbr, ESP32MiniDrop-B_Mask.gbr, ESP32MiniDrop-B_SilkS.gbr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]
2020-08-30 update silkscreen color to black
2020-08-31 add Stand source files
    [ESP32MiniDrop_Stand_BottleAdapter.stl, ESP32MiniDrop_Stand_CounterWeight.FCStd, ESP32MiniDrop_Stand_CounterWeight.stl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]
2020-09-01 update stand files and readme
    [ESP32MiniDrop_Stand_SolenoidBracket.FCStd, ESP32MiniDrop_Stand_TripodClampTop.FCStd]
2020-09-01 Update Solenoid Bracket Geometry
    [ESP32MiniDrop_Stand_SolenoidBracket.FCStd, ESP32MiniDrop_Stand_SolenoidBracket.stl]
2020-09-01 Add Rod Clip and Rod End
    [ESP32MiniDrop_Stand_RodClip.FCStd, ESP32MiniDrop_Stand_RodClip.stl, ESP32MiniDrop_Stand_RodEnd.FCStd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]
2020-09-02 Add Snap version of Solenoid Bracket
    [ESP32MiniDrop_Stand_SolenoidBracketSnap.FCStd]
2020-09-02 Add stl file SolenoidBrackSnap
    [ESP32MiniDrop_Stand_SolenoidBracketSnap.stl]
2020-09-04 Update Geometry
    [ESP32MiniDrop_Stand_TripodClampTop.FCStd]
2020-09-04 Clean up & connected LED
2020-09-04 Reduce Size
    [ESP32MiniDrop_Stand_SolenoidBracketSnap.FCStd]
2020-09-04 Update Geometries
    [ESP32MiniDrop_Stand_SolenoidBracketSnap.stl, ESP32MiniDrop_Stand_TripodClampTop.stl]
2020-09-04 add holding solenoid function
2020-09-05 Add polygon pour to VREG IN
    [ESP32MiniDrop.kicad_pcb]
2020-09-05 Update RodEnd Geometry
    [ESP32MiniDrop_Stand_RodEnd.FCStd, ESP32MiniDrop_Stand_RodEnd.stl]
2020-09-05 Add blue LED function
2020-09-05 fix shutter control hookup
    [ESP32MiniDrop.kicad_pcb, ESP32MiniDrop.sch]
2020-09-06 Switch Shutter & Focus (for canon)
2020-09-07 Fix pin mapping error on Q1, Q2
    [ESP32MiniDrop.kicad_pcb, ESP32MiniDrop.sch]
2020-09-07 Fix transistor Q3 gate connection
    [ESP32MiniDrop.kicad_pcb]
2020-09-08 change solenoid control to pin 8 GPIO32
2020-09-08 Change mounting holes to M3, update tracks, change solenoid control to pin 8 of ESP32
    [ESP32MiniDrop.kicad_pcb, ESP32MiniDrop.sch]
2020-09-09 Add Solenoid Nozzle
    [ESP32MiniDrop_Stand_SolenoidNozzle.FCStd]
2020-09-09 update Solenoid Bracket CAD file
    [ESP32MiniDrop_Stand_SolenoidBracket.FCStd]
2020-09-09 Add Solenoid Nozzle STL
    [ESP32MiniDrop_Stand_SolenoidNozzle.stl]
2020-09-09 Update Solenoid Bracket STL
    [ESP32MiniDrop_Stand_SolenoidBracket.stl]
2020-09-09 Increase nut clearance
    [ESP32MiniDrop_Stand_RodEnd.FCStd, ESP32MiniDrop_Stand_RodEnd.stl]
2020-09-09 Update Top Tripod Bracket geometry
    [ESP32MiniDrop_Stand_TripodClampTop.FCStd]
2020-09-19 fix Solenoid MOSFET Pin Mapping
    [ESP32MiniDrop.kicad_pcb, ESP32MiniDrop.sch]
2020-09-19 section off Do Not Place parts
    [ESP32MiniDrop.sch]
2020-09-20 Remove USB to UART components
    [ESP32MiniDrop.sch]
2020-09-20 Unroute USB to UART components
    [ESP32MiniDrop.kicad_pcb]
2020-09-20 Update passives to all 1206, unroute and reposition
    [ESP32MiniDrop.kicad_pcb, ESP32MiniDrop.sch]
2020-09-20 Reroute components
    [ESP32MiniDrop.kicad_pcb]
2020-09-20 Attach Pair Switch to ESP32 IO0 for boot mode selection
    [ESP32MiniDrop.kicad_pcb, ESP32MiniDrop.sch]
2020-09-20 Update Component MPN and Values
    [ESP32MiniDrop.kicad_pcb, ESP32MiniDrop.sch]
2020-09-20 Change barrel jack part, update routing
    [ESP32MiniDrop.kicad_pcb, ESP32MiniDrop.sch]
2020-09-20 Update Gerbers
    [ESP32MiniDrop-B_Cu.gbr, ESP32MiniDrop-B_Mask.gbr, ESP32MiniDrop-B_SilkS.gbr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]
2020-09-21 Change Audio Jack to SJ1-3523N
    [ESP32MiniDrop.kicad_pcb, ESP32MiniDrop.sch]
2020-09-21 Update 3.3V trace routing
    [ESP32MiniDrop.kicad_pcb]
2020-09-21 Change libraries to relative project library
    [ESP32MiniDrop.kicad_pcb]
2020-09-21 Update library paths
    [ESP32MiniDrop.sch]
2020-09-26 Refresh Gerbers
    [ESP32MiniDrop-B_Cu.gbr, ESP32MiniDrop-B_Mask.gbr, ESP32MiniDrop-B_SilkS.gbr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]
2020-09-26 Fix missing library item
    [ESP32MiniDrop.kicad_pcb, ESP32MiniDrop.sch]
2020-09-30 Add logo and update PCBA Rev
    [ESP32MiniDrop.kicad_pcb]
